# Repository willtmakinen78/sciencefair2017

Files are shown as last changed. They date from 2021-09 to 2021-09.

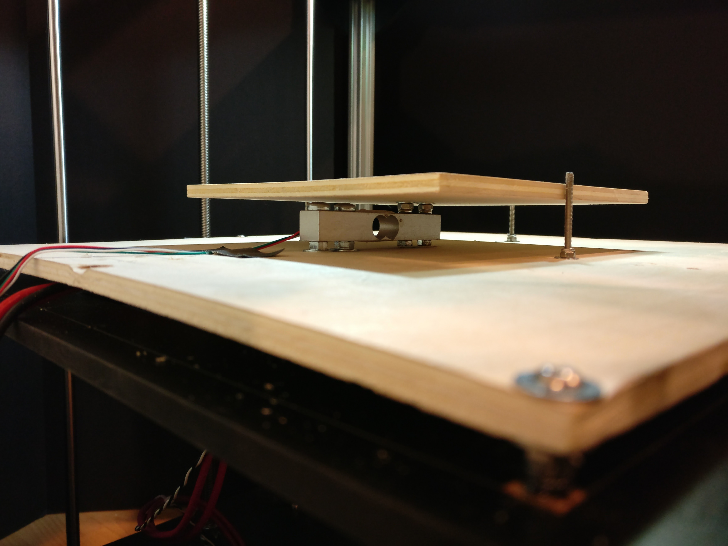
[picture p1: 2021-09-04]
pics/7.Load_NoBed_Side.jpg

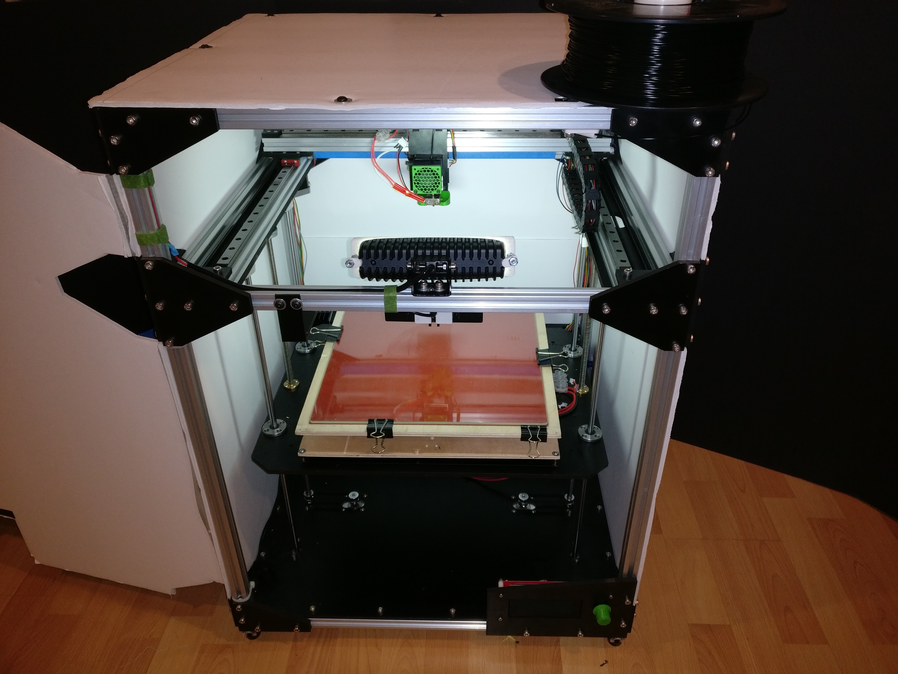
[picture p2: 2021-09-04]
pics/1.Title.jpg

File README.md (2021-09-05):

# Science Fair 2017
Listed in this repository are some of the files used for the development of my highschool Junior year science fair project, in which I characterized the an FDM 3D printing process in real time.

This project was an extension of the work started the previous summer at the NASA Langely Research Center with Dr. Godfrey Sauti. The goal was to add sensors to an FDM 3D printer to detect errors in real time, allowing the print to either be stopped or correcting for them and continuing the print. More details can be seen in the `Poster.pdf` file, however a brief rundown of each sensor/error detection system is provided below:

### Load Cell: Layer Adhesion
The entire print bed was mounted on top of a load cell. This measuered changes in force upon the print bed to be measured each layer, allowing for layer adhesion errors to be detected. This is because as the print layers peeled up (either from the bed or in the middle of the part), the would push against the print head as it passed over them, resulting in a spike in force. If this happened too many layers in a row, the print head and print bed temperatures would be increased in order to promote better adhesion and remedy the problem.

### Camera: General Print Errors
This detection method was geared towards industrial applications, in which many copies of an object might be printed at once. First, a calibration print would be run, where care would be taken to ensure optimal printing. During this print, a camera would take pictures every few layers, and stored as reference images. Then, when the subsequent "production" prints were run, pictured would be taken at identical points during the prints and compared to the reference pictures (all other aspects of the pictures, such as the background, lighting, etc. would remain constant). After performing some pixel math, the number of different pixels was calculated. If the number of different pixels reached a predefined threshold, the print was declared a failure and the user notified.

This portion of the project resulted in a Patent, No. 11,084,091. A PDF of it is visible in the file `Patent.pdf`.

### Laser + Photoresistors: 
This system was designed to detect print peeling as well. After each layer, a laser pointer connected to the extruder would scan across the entire x-axis pointing at an array of photoresistors. It was situated at a height such that any layer peeling or print artifacts, due to bad bed adhesion, improper print temperature, etc. would block the laser pointer, resulting in a change in resistance across the photoresistors. Again, if this change occurred too many times in a row, an error was declared and a notification sent to the user.

## System Overview
Aside from the sensors themselves, the error detection system consisted of 3 main components: a host computer running a java program, an arduino reading all of the sensors, and the printer itself. The java program served as the host. It was responsible for sending gcode commands to the printer, including special ones when a picture or, loadcell reading, or laser pointer scan needed to be taken. It also processed the camera and sensor inputs and determined if the print was failed or not, attempting to remedy it or communicating with the web interface to notify the user (note that also included are some python files that were initially used to modify the gcode coming from the slicer and command the printer to perform specific moves. The arduino interfaced directly with the sensor and 3d printer hardware, sending preprocesed inputs to the host computer, while the printer did the actual printing and movement. This description can be seen in more detail in the `flow` folder.

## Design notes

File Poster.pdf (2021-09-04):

# Real-Time 3D Printing Error Detection and Correction

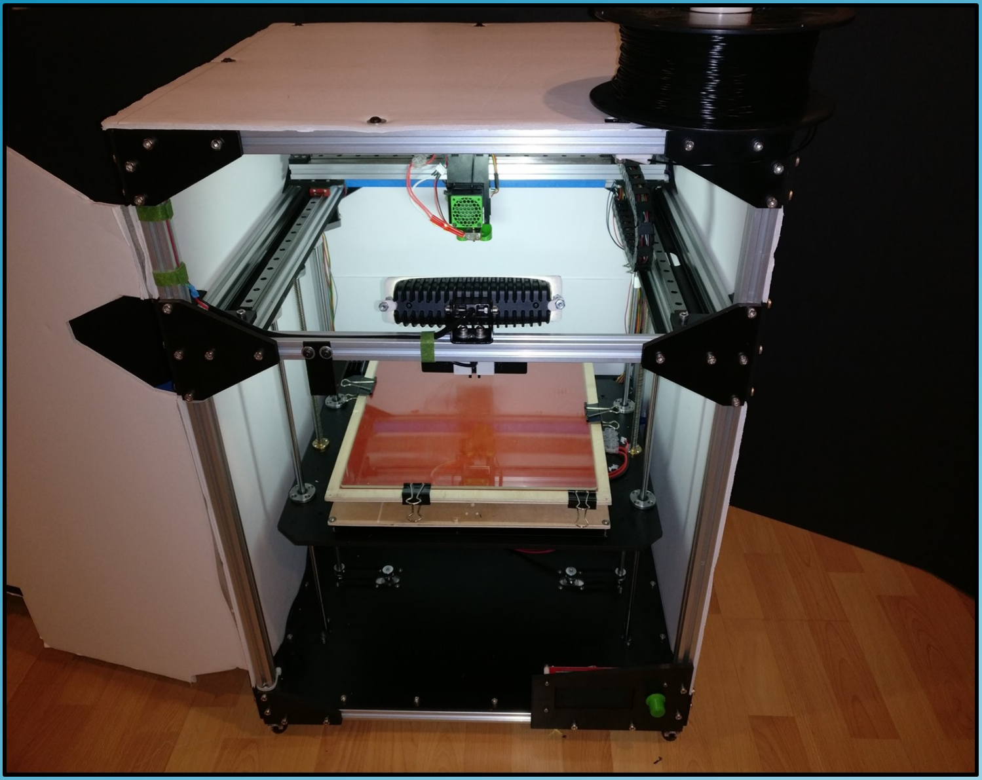
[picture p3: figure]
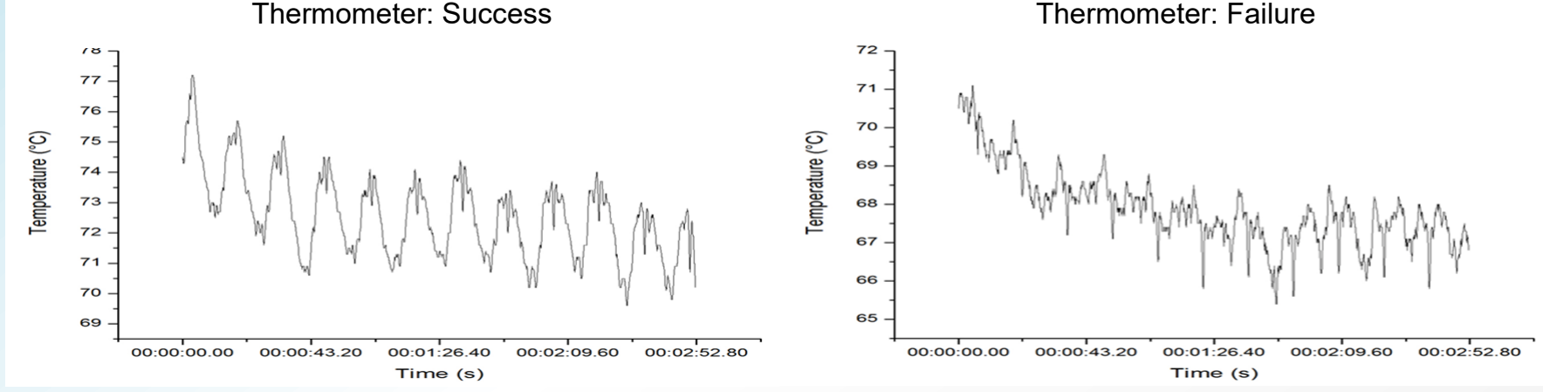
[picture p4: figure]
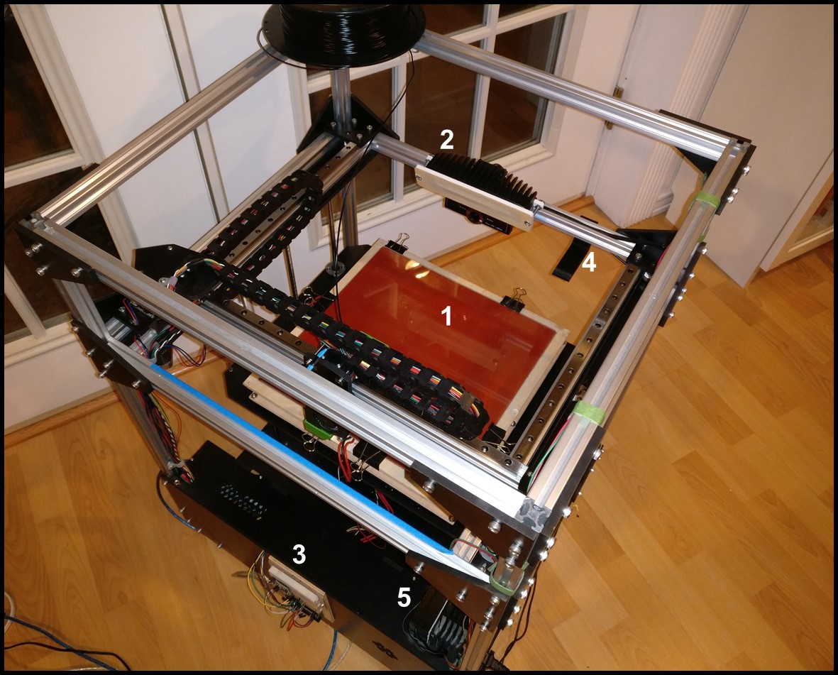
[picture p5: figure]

# Background

- Fused Filament Fabrication (FFF) is an Additive Manufacturing (AM) process that creates objects by laying down successive layers of molten material according to a CAD drawing
- FFF is capable of replicating much more complex designs more efficiently than traditional subtractive manufacturing techniques, such as milling
- FFF or 3D printing machines are easily accessible and have become popular in hobbyist/ prototyping environments
- Once exported to the appropriate format, the CAD file is sent through slicing software, generating the G-Code commands that will be sent to the printer

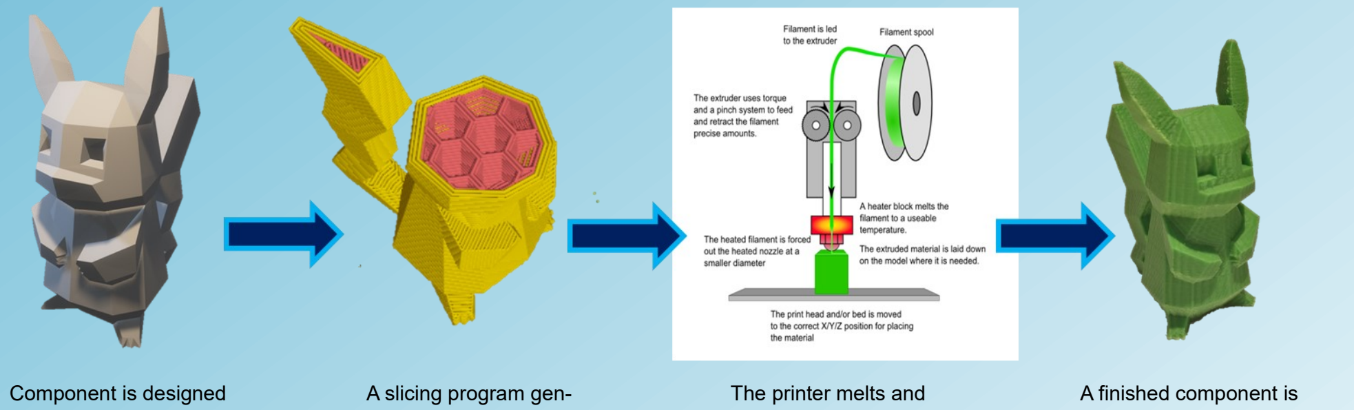
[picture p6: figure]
Component is designed; A slicing program gen-; The printer melts and; A finished component is

# Purpose

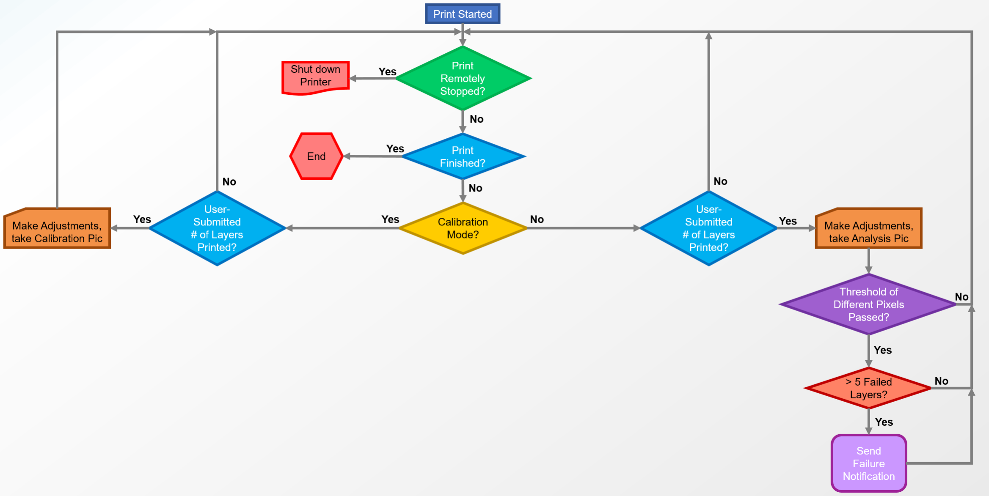
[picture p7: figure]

- Current 3D printers are primarily open-loop systems; sensors to introduce feedback into the printing process are nonexistent
- Consistent, high-quality prints currently only achievable on costly, professional FFF machines. Even these rarely utilize process monitoring
- Adding sensors to monitor the print process in real time can ensure consistently acceptable parts even on low-end machines

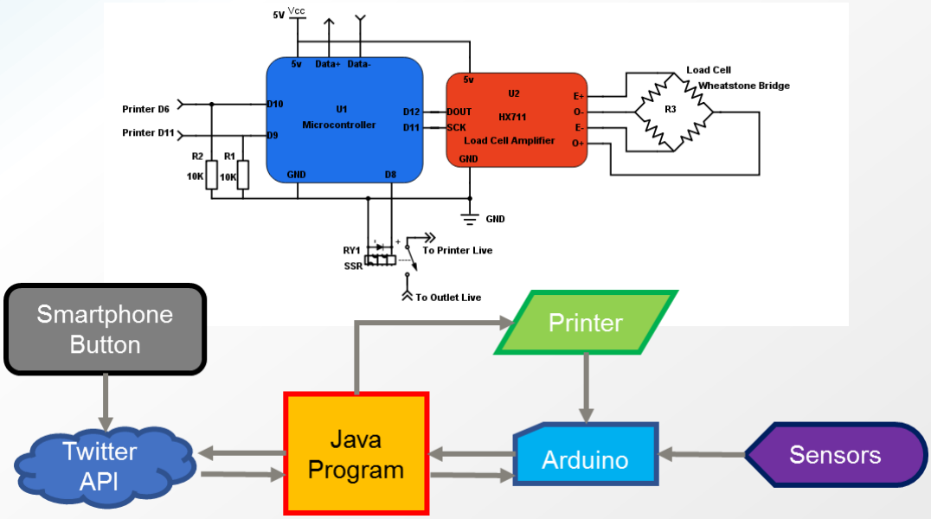
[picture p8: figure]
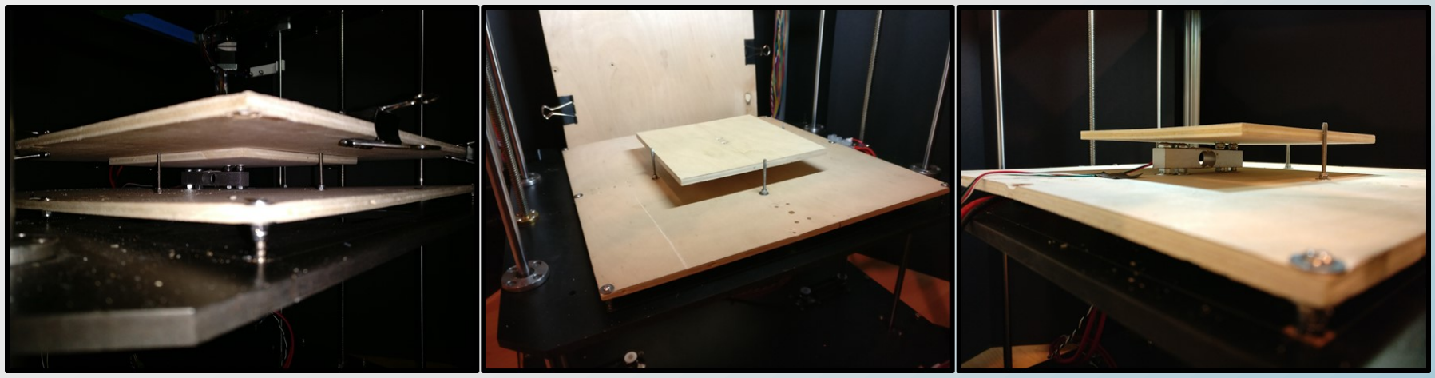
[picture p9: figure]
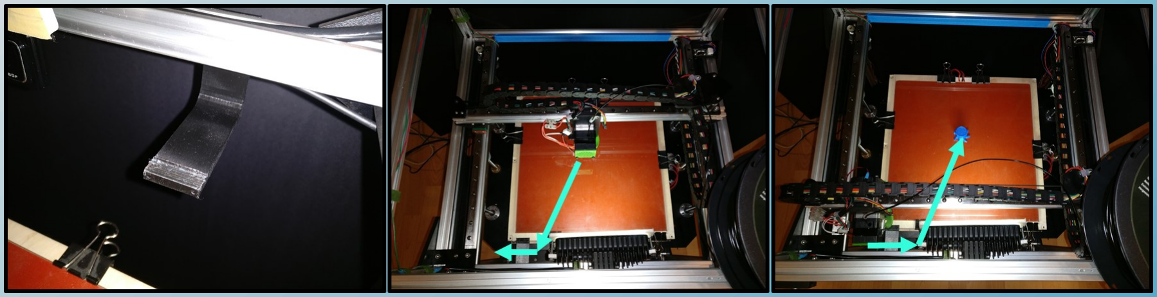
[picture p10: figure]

# Future Directions

- Improve load cell vibration isolation
- More advanced computer vision techniques, additional camera angles
- Integrate multiple sensor arrays into a single system
- Additional sensor types
- In-situ G-Code generation
Adhesion Failure: | Layer Shifting:

Feeding Failure:

Improper Melt Pool Temperature:

Others:

# Common 3D Printing Errors

Photo: Simplify3D

Photo: Simplify3D

Photo: Android Central

Photo: Simplify3D

Photo: Simplify3D

# William Makinen

# Characterization Setup

- Four sensor sets were initially tested to determine which ones would be the most viable options for a real time sensing system
- The camera and the load cell proved to be the most reliable and robust options, allowing for the detection of a variety of errors while remaining inexpensive and simple to implement
Camera: | Test Object:

Load Cell:

IR Thermometer:

Profilometer:

The test object used with each sensor setup | Slips of paper inserted in between two layers to emulate a failure

The profilometer’s laser dot measuring extruded material

Full profilometer setup

Profilometer: Success | Profilometer: Failure
Thermometer: Success | Thermometer: Failure
Successful thermometer print data | Failed thermometer print data

Failed Print

The thermometer data was correlated with that of a thermal camera

Load Cell: Success | Load Cell: Failure

Thermometer setup

Successful Print | Result after comparing Images

# Diagram

### 1. Load Cell:

### 2. Camera Assembly:

### 4. Wiper:

### 3. Microcontroller:

### 5. SSR:

The camera is mounted in the front of the printer to avoid capturing the unintentional movement of the print head assembly. The light (switched off here), illuminates the target to ensure consistent lighting from shot to shot.

The wiper is used to clean up extruder ooze produced when the bed or extruder temperature is increased and every time the camera takes a picture. Located at the front of the printer, a wipe is performed before (middle) and after (right) each action.

The solid state relay (SSR) shuts down the printer when instructed by the user

Located underneath the heated build plate, the load cell detects failures in adhesion by measuring variances in the extruder's pressure on the bed

The microcontroller, mounted on the back of the printer, is responsible for communicating the printer’s actions to the Java program.

# Camera Filter

# Schematic

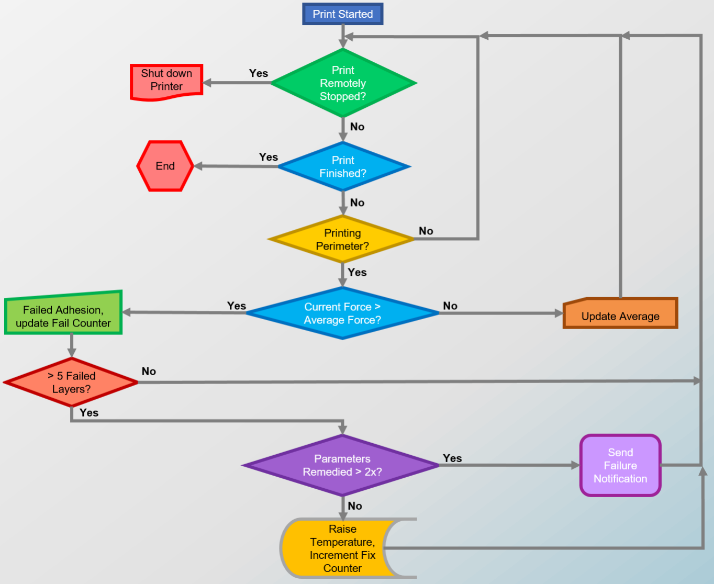
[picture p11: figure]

# Materials

- Wheatstone bridge load cell
- Load cell amplifier
- Webcam
- Solid-state-relay
- Microcontroller
- USB connectors
- Miscellaneous electrical components (wire, pull-up resistors, transistor, etc.)

Total Cost Before Printer: ~$70

using CAD Software

erates G-Code
extrudes material

produced

All images not otherwise credited were produced by William Makinen

Camera Flow Diagram | Load Cell Flow Diagram

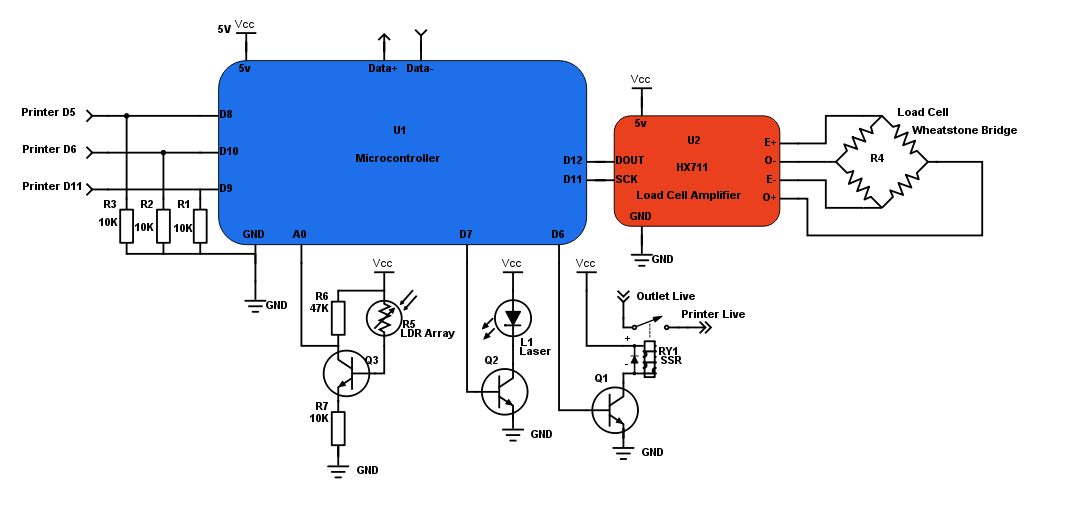
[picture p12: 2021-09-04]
wiring/Schematic.png

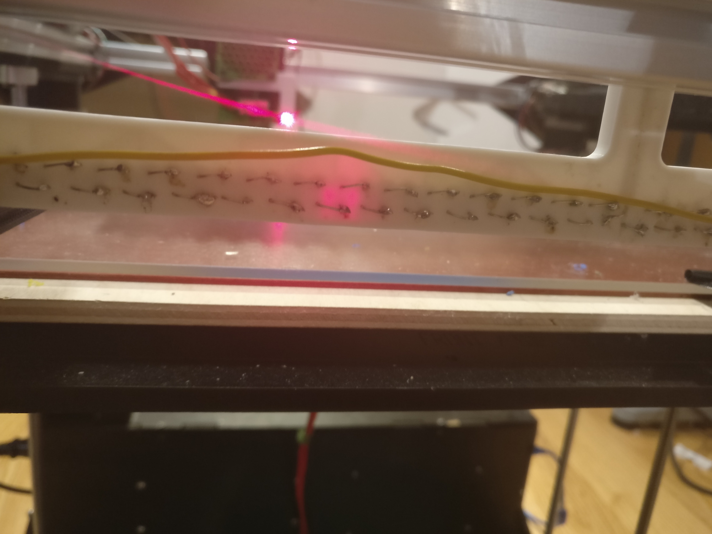
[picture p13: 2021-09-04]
pics/20.Laser7.jpg

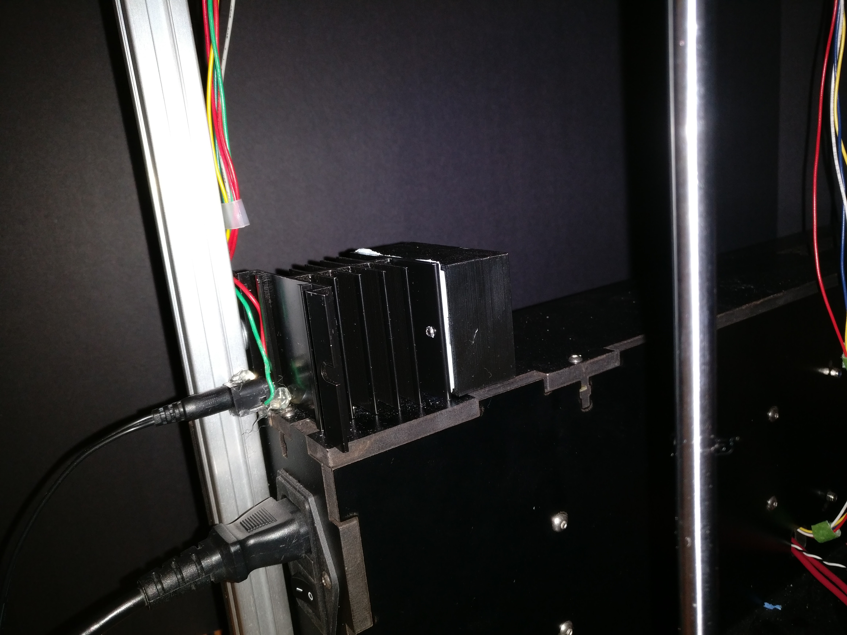
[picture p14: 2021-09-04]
pics/13.SSR.jpg

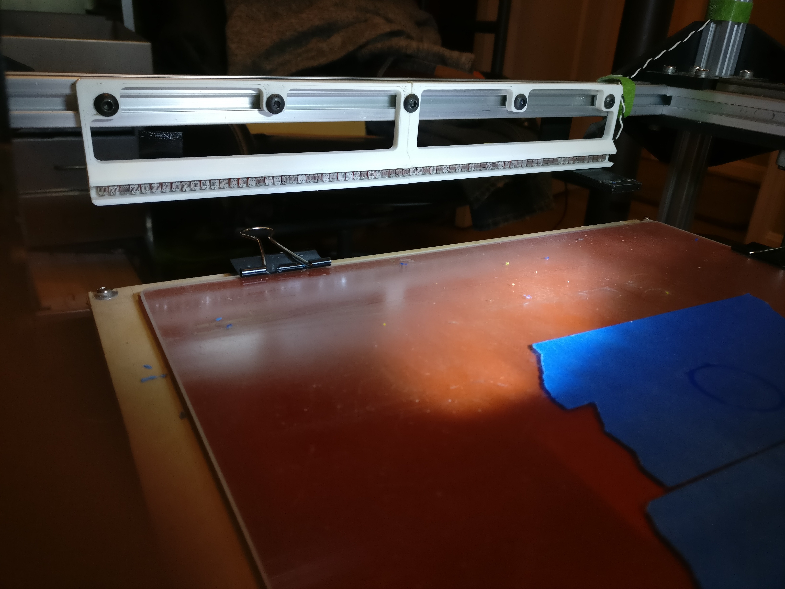
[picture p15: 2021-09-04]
pics/15.Laser2.jpg

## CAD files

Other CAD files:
cad/Proximity Sensor Mount.dwg
cad/Camera_Bed_Detector.ipt
cad/Camera_Display_Box.ipt
cad/Camera_Mount.ipt
cad/Camera_Wiper.ipt
cad/Clamp.ipt
cad/Cone.ipt
cad/Frame.ipt
cad/LDR_Holder.ipt
cad/LDR_Holder_1.ipt
cad/Laser_Holder.ipt
cad/Laser_Holder_1.ipt
cad/Light Diffusor.iam
cad/Ooze_Ramp_Bottom.ipt
cad/Ooze_Ramp_Top.ipt
cad/Proximity Sensor Mount.ipt
cad/Proximity Sensor Mount_1.ipt
cad/Tower.ipt

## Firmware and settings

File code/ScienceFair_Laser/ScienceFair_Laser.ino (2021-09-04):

const int lightPin = 0;                                 //pin assignments
const int detectPin = 8;
const int laserPin = 7;
const int shutDownPin = 6;
const int lf = 10;                                          //used for sending the signals

int pass = 0;
int acknowledged = 0;

void setup() {
  Serial.begin(9600);
  pinMode(detectPin, INPUT);
  pinMode(laserPin, OUTPUT);
  pinMode(shutDownPin, OUTPUT);

  digitalWrite(laserPin, LOW);
  digitalWrite(shutDownPin, HIGH);
}
void loop() {
  if (digitalRead(detectPin) == HIGH) {
    switch (pass) {
      case 0:
        pass = 1;
        break;
      case 11:
        pass = 2;
        break;
      case 22:
        pass = 3;
        break;
    }
  }
  else {
    switch (pass) {
      case 1:
        pass = 11;
        break;
      case 2:
        pass = 22;
        break;
      case 3:
        pass = 0;
        break;
    }
  }
  switch (pass) {
    case 0:
      Serial.println("NoScan");
      break;
    case 1:
      if (acknowledged == 1) {
        Serial.print(analogRead(lightPin));
        Serial.write(lf);
      }
      else {
        Serial.print("P1");
        Serial.write(lf);
      }
      break;
    case 2:
      if (acknowledged == 2) {
        Serial.print(analogRead(lightPin));
        Serial.write(lf);
      }
      else {
        Serial.print("P2");
        Serial.write(lf);
      }
      break;
    case 3:
      if (acknowledged == 3) {
        Serial.print(analogRead(lightPin));
        Serial.write(lf);
      }
      else {
        Serial.print("P3");
        Serial.write(lf);
      }
      break;
    case 11:
      Serial.println("trans");
      break;
    case 22:
      Serial.println("trans");
      break;
  }
  //  Serial.print(analogRead(lightPin));
  //  Serial.write(lf);
  //  Serial.print("scaNot");
  //  Serial.write(lf);
  if (Serial.available()) {
    char temp = Serial.read();
    switch (temp) {                                 //shut down and restart the printer when instructed by proecssing
      case 's':
        digitalWrite(shutDownPin, LOW);
        break;
      case 'g':
        digitalWrite(shutDownPin, HIGH);
        break;
      case 'e':
        acknowledged = 0;
        break;
      case 'o':
        acknowledged = 1;
        break;
      case 't':
        acknowledged = 2;
        break;
      case 'r':
        acknowledged = 3;
        break;
      case 'l':
        digitalWrite(laserPin, HIGH);
        break;
      case 'c':
        digitalWrite(laserPin, LOW);
        break;
    }
  }
}

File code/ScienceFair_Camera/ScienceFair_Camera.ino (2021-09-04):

const int bedDetector = 10;                                 //pin assignments
const int shutDownPin = 6;
const int lf = 10;                                          //used for sending the signals

long startMillis;

void setup() {                                              //initialization
  Serial.begin(9600);
  pinMode(bedDetector, OUTPUT);
  pinMode(shutDownPin, OUTPUT);

  digitalWrite(shutDownPin, HIGH);

  startMillis = millis();
}
void loop() {
  if (millis() - startMillis > 100) {
    if (digitalRead(bedDetector) == HIGH) {                   //if the bed is in the camera position:
      Serial.print("pic");                                        //send the appropriate signal
      Serial.write(lf);
    }
    else {
      Serial.print("print");                                        //otherwise send the other signal
      Serial.write(lf);
    }
    startMillis = millis();
  }
  if (Serial.available()) {
    char temp = Serial.read();
    if (temp == 's') {                                      //shut down and restart the printer when instructed by proecssing
      digitalWrite(shutDownPin, LOW);
    }
    else if (temp == 'g') {
      digitalWrite(shutDownPin, HIGH);
    }
  }
}
